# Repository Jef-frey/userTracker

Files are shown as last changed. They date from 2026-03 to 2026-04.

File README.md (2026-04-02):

# User tracker using IR sensors
This project contains the software and design to build a device that will rotate in response to the user's hand movement, such that it follows or avoids the user's hand. This is used in a hobby project of mine to add on to a robot model.

## Components
IR transmitters and receivers will be used to detect the user's hand movement, a motor will be used such that the device follows the user's hand. A LED will be used to simulate the eye of the device. And PIC16F15344 will be used to control the signals.

- 1 x PIC16F15344
- 1 x 28BYJ-48 Stepper Motor
- 1 x yellow LED
- 2 x IR receivers
- 2 x IR transmitters
- 3 x 1 kOhm current-limiting resistor
- 2 x 10 kOhm resistor

## Design
A pair of IR transmitter/receiver will be used to create a sensor to detect how close the user's hand is to the device.
Two such sensors will be used to compare the distance of the sensors and the user's hand, and the device will be mounted on a motor to rotate in the direction corresponding to the user's proximity with the sensors. 

https://github.com/user-attachments/assets/1b537696-194a-400e-b10d-6a0f2009ed03

## Configuration
The circuit and PCB will need to be redesigned to add features or change to fit your own project, but if you wish to just try out the design, the PCB can be glued to the motor and it will function as intended.
You may want to change the sensitivity of the device, the steps are as follow:
1. determine locations of the 'rec_1' and 'rec_2' points on your own circuit ('rec_1' and 'rec_2' will be shown at the schematic below)
2. put your hand at the distance for the desired movement detection range and measure the voltage at the 'rec_1' and 'rec_2' points
3. pick the greater voltage value (in mV) from the two points, divide it by 2 and convert it to a binary number, round up the 2 least significant bits and logical right shift by 2
4. change the ADCRESH_REG variable at line 27 at the [main.c](main.c) file to the value from step 3

For example, in my device I measured 363mV  
363mV -> 181.5 -> 0b1011_0101 -> 0b1011_1000 -> 0b0010_1110  
And '0b00101110' is my value for ADCRESH_REG

## Schematic
circuit_schematic
circuit_pcb

## Microcontroller requirements
A different microcontroller can be used, but it have to support the following features/peripherals
- timer
- comparator
- PWM (uses a second timer in this example)
- ADC

## How it works
The device has 3 states: IDLE, CW, CCW  
In IDLE state, motor will stop, LED will fade off if it was on(TMR0 will slowly decrement the duty cycle of the PWM). Comparator will be used to compare voltage difference between IR receivers, the change in output will turn on the LED to start fading on(TMR0 will slowly increment the duty cycle of the PWM), and device will enter CW(clockwise) state or CCW(counter-clockwise) state depends on the comparator output.  
In CW state, motor will turn clockwise, and ADC will continuously detect IR receivers' voltage level. Once both receivers' voltage level is lower than specific level for a few cycles (to avoid misread), device will enter IDLE state.  
In CCW state, motor will turn counter-clockwise, all other operations are the same as CW state.

## Possible issues and improvements
- A different sensor was originally used, as the current detection method has very limited range. The first iteration used PIR sensors, but it cannot be used on moving devices and has a ~2 sec delay time after motions stopped so it wasn't used. Upon further research time of flight sensor may be used, but it is more costly and complex.
- To save power in IDLE mode, a sleep function can be implemented
- To save power in IDLE mode, IR transmitter can be turn on for a short interval after a small delay (to have a PWM on the IR transmitter)

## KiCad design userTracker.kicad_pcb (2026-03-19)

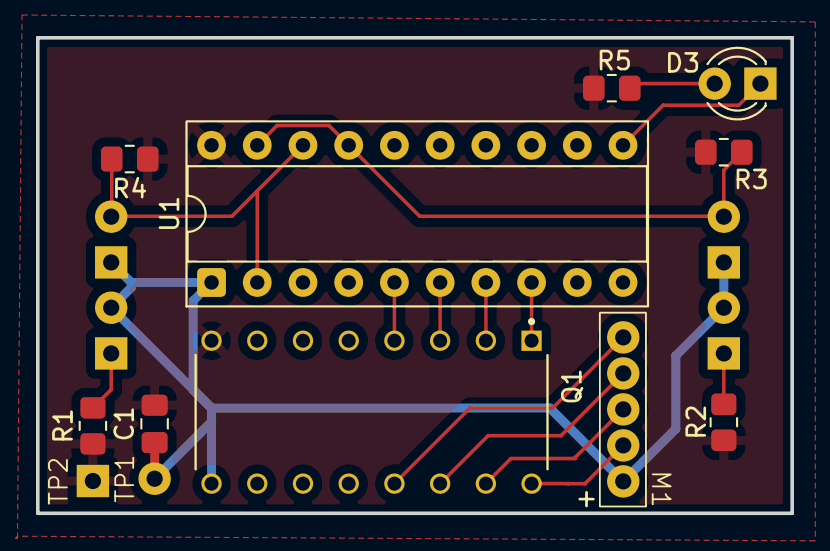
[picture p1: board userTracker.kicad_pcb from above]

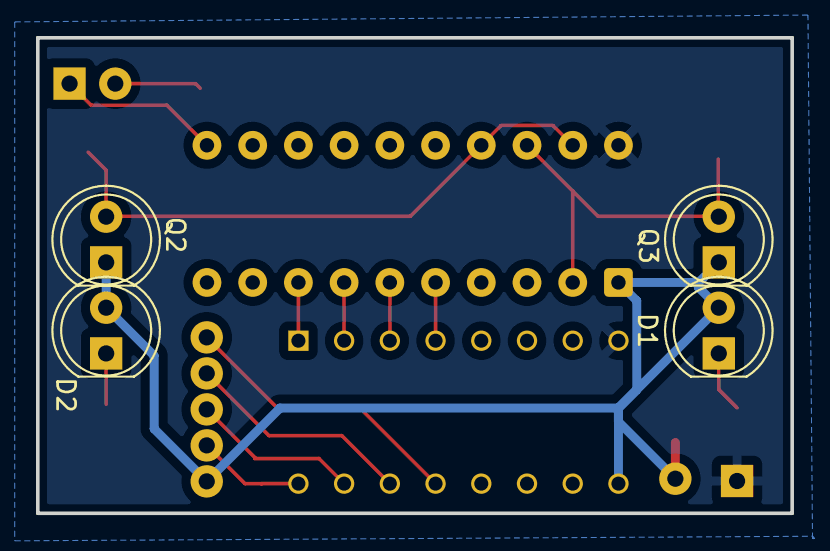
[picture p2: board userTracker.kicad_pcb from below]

Board: 2 copper layers, 41.9 x 26.4 mm, 16 parts (4 on the bottom side), 16 nets.

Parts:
C1: 0.1uF; C_0805_2012Metric_Pad1.18x1.45mm_HandSolder
D1, D2: IR transmitter; LED_D5.0mm_Clear
D3: LED; LED_D3.0mm
M1: 28BYJ-48; stepper_motor
Q1: ULN2003AN; DIP794W45P254L1969H508Q16
Q2, Q3: IR receiver; LED_D5.0mm_IRBlack
R1, R2, R5: 1 kOhm; R_0805_2012Metric_Pad1.20x1.40mm_HandSolder
R3, R4: 10 kOhm; R_0805_2012Metric_Pad1.20x1.40mm_HandSolder
TP1, TP2: TestPoint; test_point
U1: PIC16F15344; DIP-20_W7.62mm_Socket

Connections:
+5V: C1.1, D1.2 (A), D2.2 (A), M1.1, Q1.9, Q2.1, Q3.1, TP1.1, U1.1 (VDD)
/PWM: D3.1 (K), U1.11 (RB6)
/RC3: Q1.2, U1.7 (RC3)
/RC4: Q1.3, U1.6 (RC4)
/RC5: Q1.4, U1.5 (RC5)
/RC6: Q1.1, U1.8 (RC6)
/m1: M1.2, Q1.16
/m2: M1.3 (-), Q1.15
/m3: M1.4, Q1.14
/m4: M1.5, Q1.13
/rec_1: Q2.2, R3.2, U1.17 (RA2), U1.19 (RA0/ICSPDAT)
/rec_2: Q3.2, R4.2, U1.2 (RA5), U1.18 (RA1/ICSPCLK)
GND: C1.2, Q1.8 (E), R1.1, R2.1, R3.1, R4.1, R5.2, TP2.1, U1.20 (VSS)
unnamed: D1.1 (K), R1.2
unnamed: D2.1 (K), R2.2
unnamed: D3.2 (A), R5.1

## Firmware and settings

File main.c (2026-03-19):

/* 
 * File:   main.c
 * Author: Jeffrey
 * Date: July 21, 2025, 9:24 AM
 * Purpose: Use hand motion to turn the head of a model
 * and fade on and off a LED using IR detection
 */

/*
 * motor: total step per rotation = t = 256 * 60
 * 
 * pin layout:
 *  - receiver1 => RA0, RA2
 *  - receiver2 => RA1, RA5
 *  - EYE_LED   => RB6
 *  - motor     => RC3-6
 *  
 */

#include <xc.h>

#define _XTAL_FREQ 31000U //Specify the XTAL crystal FREQ 31kHz

#pragma config WDTE = OFF       // WDT operating mode (WDT Disabled, SWDTEN is ignored)

const int STEP_REV = 2048;      // steps per revolution
const int ADCRESH_REG = 0b00101110;    // setting the threshold sensor, currently ~368mV
// for the ADC result register high

int fade_on = 1; // indicate if LED fades on or off
int adc_rdy = 0; // flag for ADC's Acquisition Time wait time in TMR0
int rev_st_clr;  // flag for first receiver reads 0V
int rev_nd_clr;  // flag for second receiver reads 0V
int adc_cnt = 0;

enum motor_state {
    IDLE,
    CW,
    CCW
};

enum motor_state state;

void TMR0_rst() {
//    period = 209 us
    TMR0H = 0xF3;
    TMR0L = 0xFF;
}

void TMR0_Initialize(){
    PIR0bits.TMR0IF = 0;
	PIE0bits.TMR0IE = 0;

//T0CS LFINTOSC; T0CKPS 1:2; T0ASYNC not_synchronised; 
    T0CON1 = 0x91;
    T0CON0 = 0x90;
}

void __interrupt() isr(void)
{
    if (TMR0IF) {
//        TMR0 takes care of LED fading and ADC delay
        PIR0bits.TMR0IF = 0;
        TMR0_rst();
        
//        ADC
//        cycle between input pins A2 and A5 and measure
//        after waiting for the Acquisition Time passed 
        if (adc_rdy == 0) {
            ADCON0bits.CHS = 0b000010;
        } else if (adc_rdy == 1) {
            ADCON0bits.GOnDONE = 1;
        } else if (adc_rdy == 2) {
            ADCON0bits.CHS = 0b000101;
        } else if (adc_rdy == 3) {
            ADCON0bits.GOnDONE = 1;
        }
        adc_rdy++;
        if (adc_rdy == 4) {
            adc_rdy = 0;
        }
        
//        LED PWM
        if (fade_on == 1) {
            if (PWM3DCH < 0x04){
                asm("banksel PWM3DCL");
                asm("movlw 40h");
                asm("addwf PWM3DCL,1"); //increment the LSB of PWM3DC
                asm("btfsc STATUS,0");  //if there is a carry from LSB increment
                asm("incf PWM3DCH");    //increment the MSB of PWM3DC
            }
        } else {
            // fade off until duty cycle is 0, then disable timer
            if (PWM3DCH > 0x00 || PWM3DCL > 0x00){
                asm("banksel PWM3DCL");
                asm("movlw 40h");
                asm("subwf PWM3DCL,1"); 
                asm("btfss STATUS,0");  
                asm("decf PWM3DCH");    
            } else {
                PIE0bits.TMR0IE = 0;
            }
        }
    } else if (C1IF) {
//        when motion is detected at the IR receiver
        C1IF = 0;
        ADCON0bits.ADON = 1;
        // fade on LED
        PIE0bits.TMR0IE = 1;    
        fade_on = 1;
        if (CM1CON0bits.OUT == 1) {
            state = CW;
        } else {
            state = CCW;
        }
    } else if (ADIF) {
        ADIF = 0;
    //    IDLE state if sensor's result is lower than 
    //    threshold for 4 consecutive measuring cycles, 
    //    the cycles are to make sure that there is no 
    //    motion and not just signal misread
        
        if (ADRESH <= ADCRESH_REG) {
            if (adc_rdy == 1) {
                rev_st_clr = 1;
            } else {
                rev_nd_clr = 1;
            }
        } else {
            if (adc_rdy == 1) {
                rev_st_clr = 0;
            } else {
                rev_nd_clr = 0;
            }
        }
        if (rev_st_clr == 1 && rev_nd_clr == 1) {
            adc_cnt++;
        } else {
            adc_cnt = 0;
        }

        if (adc_cnt == 4) {
            adc_cnt = 0;
//            stop measuring and turn off LED
            state = IDLE;
            fade_on = 0;
            ADCON0bits.ADON = 0;
        }
    }
}

void PWM_Initialize() {
    RB6PPS = 0x0B;  //RB6->PWM3:PWM3OUT;

    T2CON = 0x00;
    T2CLKCON = 0x01;
    T2PR = 0xD1;
    T2TMR = 0x00;
    T2CONbits.TMR2ON = 1;
    
    PWM3CON = 0x80;    
    PWM3DCH = 0x00;      
    PWM3DCL = 0x00;
    
    PWM3EN = 1;
}

void COMPARATOR_Initialize() {
    // enable comparator;non-inverting output; hysteresis enabled;async to TMR1
    CM1CON0 = 0b10000010;  
    // posedge and negedge triggered
    CM1CON1 = 0b00000011;
    CM1NCHbits.NCH = 0b000; // C1IN0-   RA1
    CM1PCHbits.PCH = 0b000; // C1IN0+   RA0
    
    // interrupt
    C1IF = 0;
    C1IE = 1;
}

void ADC_Initialize() {
// Configure the ADC module:
    ADCON1bits.ADCS = 0b011;
    ADCON1bits.ADPREF = 0b11;
    FVRCONbits.FVREN = 1;
    FVRCONbits.ADFVR = 0b10;    //FVR = 2.048V
    ADACT = 0x02;   // trigger by TMR0
    ADFM = 0;

//    interrupt
    PIR1bits.ADIF = 0;
    PIE1bits.ADIE = 1;
}

void main(void) {
//    pins initialization
    ANSELA = 0x24;
    ANSELB = 0;
    ANSELC = 0;
    TRISA = 0x27;
    TRISB = 0x00;
    TRISC = 0x00;

//  peripherals initialization
    PWM_Initialize();
    TMR0_Initialize();
    COMPARATOR_Initialize();
    ADC_Initialize();
    
    GIE = 1;
    PEIE = 1;
    
    PORTC = 0x08;
        
    state = IDLE;

    while (1) {
        if (state == CW) {
            asm("banksel PORTC");
            asm("lslf PORTC, 1");
            asm("btfss PORTC,7");
            asm("bra 2");
            asm("movlw 08h");
            asm("movwf PORTC");
            __delay_ms(1000);
        } else if (state == CCW) {
            asm("banksel PORTC");
            asm("lsrf PORTC, 1");
            asm("btfss PORTC,2");
            asm("bra 2");
            asm("movlw 40h");
            asm("movwf PORTC");
            __delay_ms(1000);
        }
    }
    
    return;
}

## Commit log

2025-10-06 Update main.c
    Update pin placement and sensor sensitivity level after feedback from installing it onto the robot model.
2026-03-19 Add files via upload
    Added the PCB files
    [userTracker.kicad_pcb, userTracker.kicad_sch]
